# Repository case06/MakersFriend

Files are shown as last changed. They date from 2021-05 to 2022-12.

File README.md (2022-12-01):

# MakersFriend

[](
    https://opensourceecology.de)

This is the source repo for the "Maker's Friend" 3D-Printer-Projekt on

https://wiki.opensourceecology.de/Maker%27s_Friend

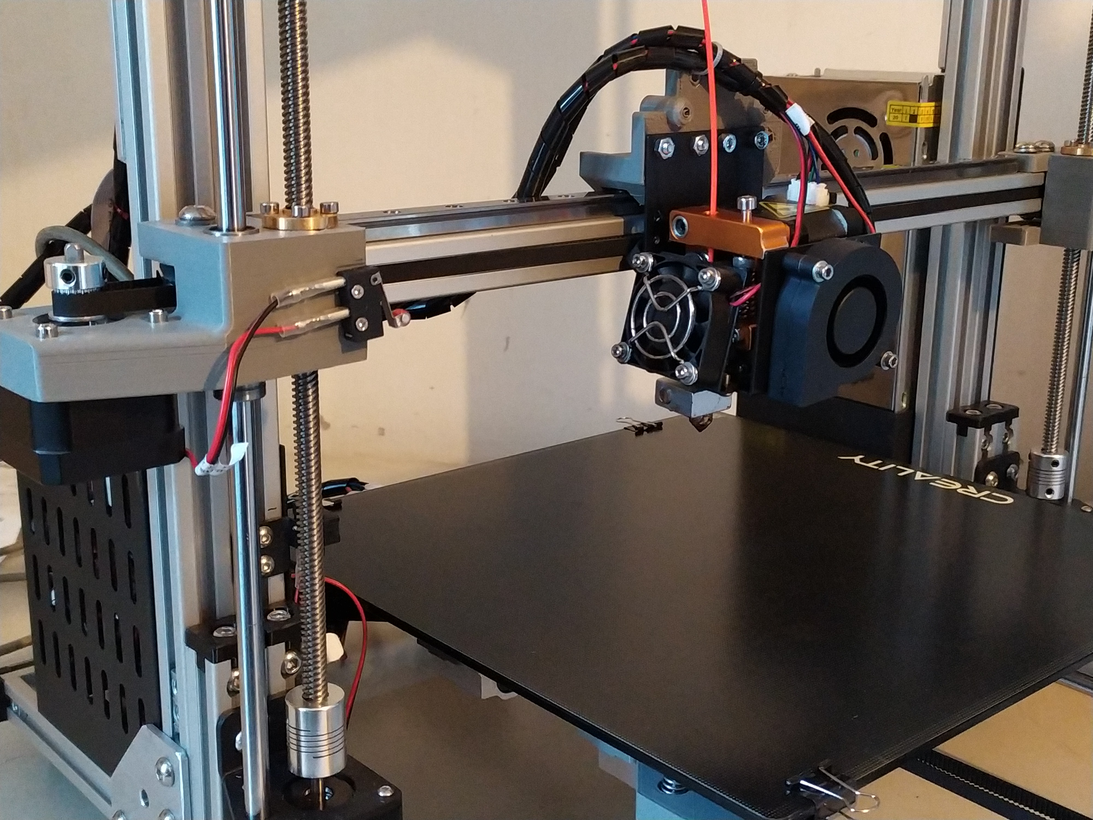
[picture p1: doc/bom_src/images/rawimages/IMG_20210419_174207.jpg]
Maker's Friend V.0.5
<p></p>

The projekt is based on the UniProKit 3D-part-library UPKlib V2.06, which is available at 

<a href="https://github.com/case06/upklib_v2"> https://github.com/case06/upklib_v2 </a>

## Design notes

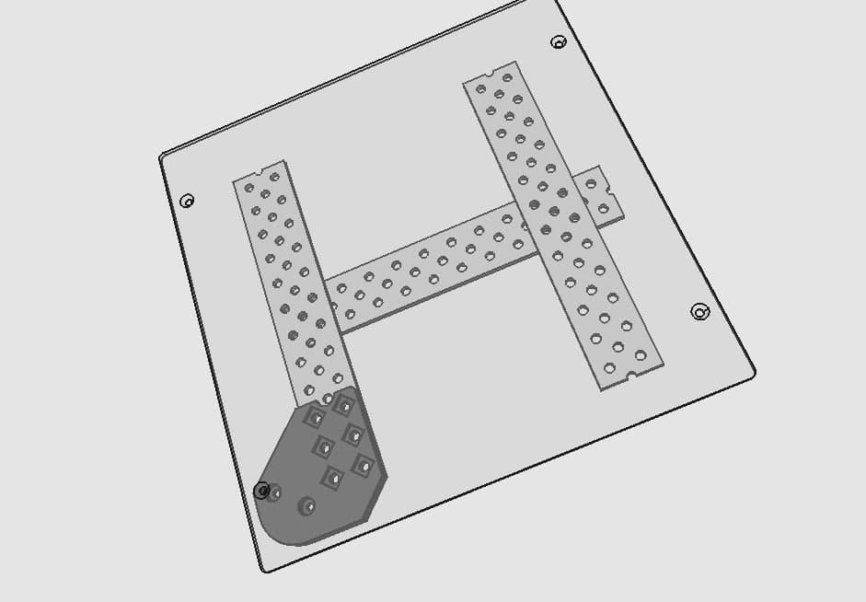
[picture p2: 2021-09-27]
cadfiles/images/heatbed/heatbed_ass.jpg

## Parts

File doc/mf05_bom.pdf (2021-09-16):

Seite 1

BOM Maker's Friend MF05 3D-Printer, UniProKit UPKlib V2.06

Partname | PartNo. | pcs. | Description | Pos | Supplier

UPKlib
tslot4 | 17092201 | 1 | T-Slot Nut 6, 40x20x20mm, framepart for tensioner | 1 | ML
tslot6 | 17092202 | 3 | T-Slot Nut 6, 60x20x20mm, distance holder | 2
tslot48 | 17092209 | 5 | T-Slot Nut 6, 480x20x20mm, distancer | 3
tslot8con | 17092220 | 2 | T-Slot Con, 480x20x20mm | 4
tslot40con_16 | | 4 | Framepart y-direction | 5
tslot48con_double | | 3 | Framepart x-direction | 6
m6x8 | 17092303 | 128 | 8mm, M6 ISO 7380, display- and spool-holder | 7
m6x12 | 17092304 | 62 | 12mm, M6 ISO 7380, mount holder | 8
m6x16 | 17092305 | 9 | 16mm, M6 ISO 7380, mount foot to frame | 9
m6x20 | 17092306 | 10 | 20mm, M6 ISO 7380, mount tslot6 | 10
m6x25cyl | 17092307 | 16 | 25mm, M6 DIN 7984, connect z-frame with y-base | 11
m6nutplate | 17092309 | 205 | für TSlot, Slot6, M6 | 12
m6washer | 17092310 | 42 | 6.4x12x1.6, DIN 125, display- and spool-holder | 13
m6nut | 17092308 | 4 | 5.6x10mm, M6 DIN934, mount z-floating-bearing | 14
m2x10 | | 2 | screws for mout limitswitch to holder | 15
m2.5x12ws | | 4 | M2.5 x 12 woodscrew | 16
m3x6 | | 17 | mount stepper | 17
m3x6cone | | 2 | mount mainboard on holder | 18
m3x8cyl | 21032807 | 20 | mount adapter on mgn12 | 19
m3x10cyl | 19070615 | 12 | mount stepper to holder | 20
m3x20cyl | 19082011 | 2 | pole for belt | 21
hammermutter_m3 | 21032803 | 16 | | 22

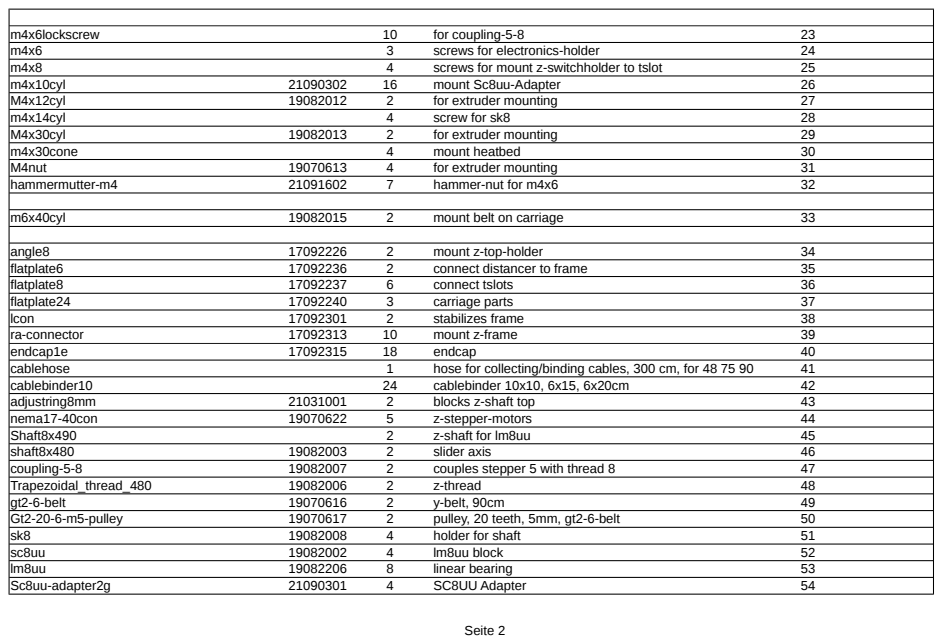
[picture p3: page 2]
Seite 2; m4x6lockscrew; for coupling-5-8; screws for electronics-holder; screws for mount z-switchholder to tslot; m4x10cyl; mount Sc8uu-Adapter; M4x12cyl; for extruder mounting; m4x14cyl; screw for sk8; M4x30cyl; m4x30cone; mount heatbed; M4nut; hammermutter-m4; hammer-nut for m4x6; m6x40cyl; mount belt on carriage; angle8; mount z-top-holder; flatplate6; connect distancer to frame; flatplate8; connect tslots; flatplate24; carriage parts; lcon; stabilizes frame; ra-connector; mount z-frame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

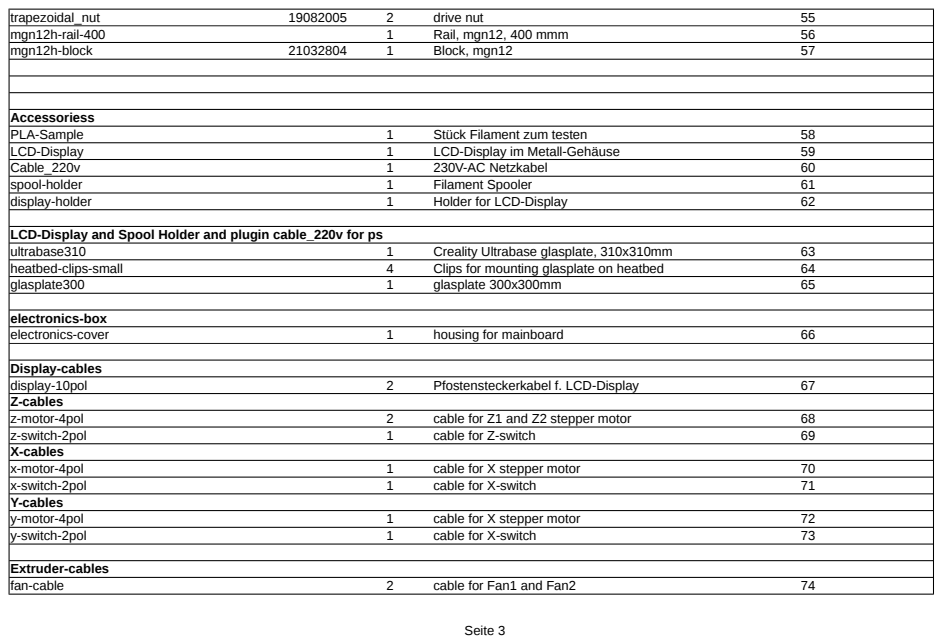
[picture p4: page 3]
Seite 3; trapezoidal_nut; drive nut; mgn12h-rail-400; Rail, mgn12, 400 mmm; mgn12h-block; Block, mgn12; Accessoriess; PLA-Sample; Stück Filament zum testen; LCD-Display; LCD-Display im Metall-Gehäuse; Cable_220v; 230V-AC Netzkabel; spool-holder; Filament Spooler; display-holder; Holder for LCD-Display; ultrabase310; Creality Ultrabase glasplate, 310x310mm; heatbed-clips-small; Clips for mounting glasplate on heatbed; glasplate300; glasplate 300x300mm; electronics-box; electronics-cover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

LCD-Display and Spool Holder and plugin cable_220v for ps

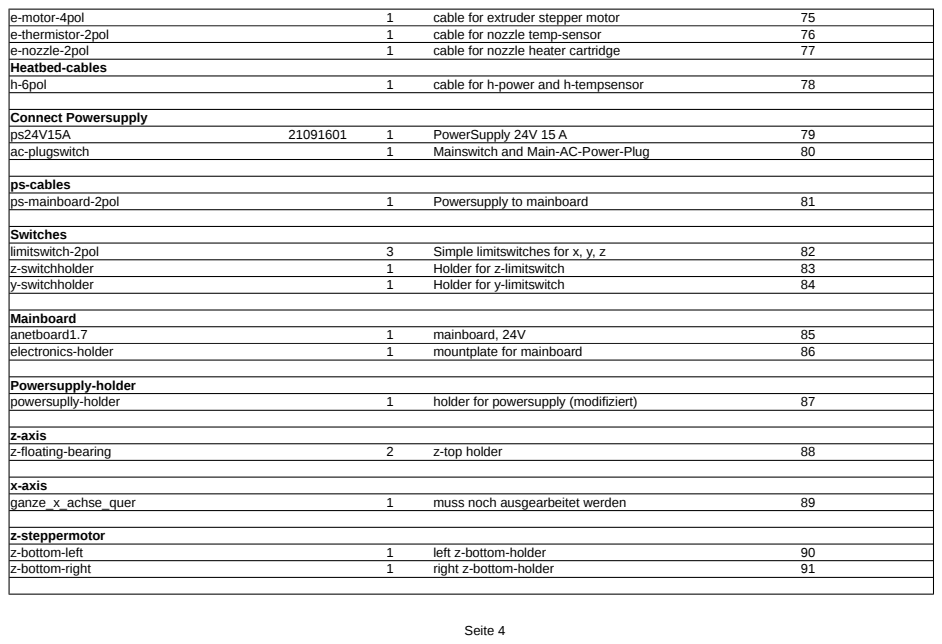
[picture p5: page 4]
Seite 4; e-motor-4pol; cable for extruder stepper motor; e-thermistor-2pol; cable for nozzle temp-sensor; e-nozzle-2pol; cable for nozzle heater cartridge; Heatbed-cables; h-6pol; cable for h-power and h-tempsensor; Connect Powersupply; PowerSupply 24V 15 A; ac-plugswitch; Mainswitch and Main-AC-Power-Plug; ps-cables; ps-mainboard-2pol; Powersupply to mainboard; Switches; limitswitch-2pol; Simple limitswitches for x, y, z; z-switchholder; Holder for z-limitswitch; y-switchholder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

Seite 5

Heatbed
heatbed300_276_209 | 1 | 300mm with hole-edge-distances 12 and 45.5 mm | 92
bedlevel-knob | 4 | adjust heatbed | 93
spring_8x25 | 4 | distance-spring for heatbed | 94
bedmount1d_left | 2 | bedmount left | 95
bedmount1d_right | 2 | bedmount right | 96

y-belt
belt-tensioner | 1 | belt-tensioner (assembly) | 97

y-steppermotor
nema17holder6mm | 1 | stepper holder, 6mm | 98

machine-feet
foot-35x24 | 4 | machine-foot, h 24 dia 35 depth 13 | 99
foot-38x25 | 0 | machine-foot, h 25 dia 38 depth 12

Extruder
extruder_adapter | 1 | extruder adapter to mount on mgn12 | 100

Mount idler
mf_idler | 1 | x-idler, z-carriage-right | 101
belt-tensioner | 1 | belt-tensioner (complete) | 102

Mount stepper
mf_steppermount | 1 | x-stepper, z-carriage-left | 103
804

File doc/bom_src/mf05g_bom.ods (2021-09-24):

BOM Maker's Friend MF05 3D-Printer, UniProKit UPKlib V2.06
Partname | PartNo. | pcs. | Description | Pos | Supplier
UPKlib
tslot4 | 17092201 | 1 | T-Slot Nut 6, 40x20x20mm, framepart for tensioner | 1 | ML
tslot6 | 17092202 | 3 | T-Slot Nut 6, 60x20x20mm, distance holder | 2
tslot48 | 17092209 | 5 | T-Slot Nut 6, 480x20x20mm, distancer | 3
tslot8con | 17092220 | 2 | T-Slot Con, 480x20x20mm | 4
tslot40con_16 |  | 4 | Framepart y-direction | 5
tslot48con_double |  | 3 | Framepart x-direction | 6
m6x8 | 17092303 | 128 | 8mm, M6 ISO 7380, display- and spool-holder | 7
m6x12 | 17092304 | 62 | 12mm, M6 ISO 7380, mount holder | 8
m6x16 | 17092305 | 9 | 16mm, M6 ISO 7380, mount foot to frame | 9
m6x20 | 17092306 | 10 | 20mm, M6 ISO 7380, mount tslot6 | 10
m6x25cyl | 17092307 | 16 | 25mm, M6 DIN 7984, connect z-frame with y-base | 11
m6nutplate | 17092309 | 205 | für TSlot, Slot6, M6 | 12
m6washer | 17092310 | 42 | 6.4x12x1.6, DIN 125, display- and spool-holder | 13
m6nut | 17092308 | 4 | 5.6x10mm, M6 DIN934, mount z-floating-bearing | 14
m2x10 |  | 2 | screws for mout limitswitch to holder | 15
m2.5x12ws |  | 4 | M2.5 x 12 woodscrew | 16
m3x6 |  | 17 | mount stepper | 17
m3x6cone |  | 2 | mount mainboard on holder | 18
m3x8cyl | 21032807 | 20 | mount adapter on mgn12 | 19
m3x10cyl | 19070615 | 12 | mount stepper to holder | 20
m3x20cyl | 19082011 | 2 | pole for belt | 21
hammermutter_m3 | 21032803 | 16 |  | 22
m4x6lockscrew |  | 10 | for coupling-5-8 | 23
m4x6 |  | 3 | screws for electronics-holder | 24
m4x8 |  | 4 | screws for mount z-switchholder to tslot | 25
m4x10cyl | 21090302 | 16 | mount Sc8uu-Adapter | 26
M4x12cyl | 19082012 | 2 | for extruder mounting | 27
m4x14cyl |  | 4 | screw for sk8 | 28
M4x30cyl | 19082013 | 2 | for extruder mounting | 29
m4x30cone |  | 4 | mount heatbed | 30
M4nut | 19070613 | 4 | for extruder mounting | 31
hammermutter-m4 | 21091602 | 7 | hammer-nut for m4x6 | 32
m6x40cyl | 19082015 | 2 | mount belt on carriage | 33
angle8 | 17092226 | 2 | mount z-top-holder | 34
flatplate6 | 17092236 | 2 | connect distancer to frame | 35
flatplate8 | 17092237 | 6 | connect tslots | 36
flatplate24 | 17092240 | 3 | carriage parts | 37
lcon | 17092301 | 2 | stabilizes frame | 38
ra-connector | 17092313 | 10 | mount z-frame | 39
endcap1e | 17092315 | 18 | endcap | 40
cablehose |  | 1 | hose for collecting/binding cables, 300 cm, for 48 75 90 64 and 20 cm | 41
cablebinder10 |  | 24 | cablebinder 10x10, 6x15, 6x20cm | 42
adjustring8mm | 21031001 | 2 | blocks z-shaft top | 43
nema17-40con | 19070622 | 5 | z-stepper-motors | 44
Shaft8x490 |  | 2 | z-shaft for lm8uu | 45
shaft8x480 | 19082003 | 2 | slider axis | 46
coupling-5-8 | 19082007 | 2 | couples stepper 5 with thread 8 | 47
Trapezoidal_thread_480 | 19082006 | 2 | z-thread | 48
gt2-6-belt | 19070616 | 2 | y-belt, 90cm | 49
Gt2-20-6-m5-pulley | 19070617 | 2 | pulley, 20 teeth, 5mm, gt2-6-belt | 50
sk8 | 19082008 | 4 | holder for shaft | 51
sc8uu | 19082002 | 4 | lm8uu block | 52
lm8uu | 19082206 | 8 | linear bearing | 53
Sc8uu-adapter2g | 21090301 | 4 | SC8UU Adapter | 54
trapezoidal_nut | 19082005 | 2 | drive nut | 55
mgn12h-rail-400 |  | 1 | Rail, mgn12, 400 mmm | 56
mgn12h-block | 21032804 | 1 | Block, mgn12 | 57
Accessoriess
PLA-Sample |  | 1 | Stück Filament zum testen | 58
LCD-Display |  | 1 | LCD-Display im Metall-Gehäuse | 59
Cable_220v |  | 1 | 230V-AC Netzkabel | 60
spool-holder |  | 1 | Filament Spooler | 61
display-holder |  | 1 | Holder for LCD-Display | 62
LCD-Display and Spool Holder and plugin cable_220v for ps
ultrabase310 |  | 1 | Creality Ultrabase glasplate, 310x310mm | 63
heatbed-clips-small |  | 4 | Clips for mounting glasplate on heatbed | 64
glasplate300 |  | 1 | glasplate 300x300mm | 65
electronics-box
electronics-cover |  | 1 | housing for mainboard | 66
Display-cables
display-10pol |  | 2 | Pfostensteckerkabel f. LCD-Display | 67
Z-cables
z-motor-4pol |  | 2 | cable for Z1 and Z2 stepper motor | 68
z-switch-2pol |  | 1 | cable for Z-switch | 69
X-cables
x-motor-4pol |  | 1 | cable for X stepper motor | 70
x-switch-2pol |  | 1 | cable for X-switch | 71
Y-cables
y-motor-4pol |  | 1 | cable for X stepper motor | 72
y-switch-2pol |  | 1 | cable for X-switch | 73
Extruder-cables
fan-cable |  | 2 | cable for Fan1 and Fan2 | 74
e-motor-4pol |  | 1 | cable for extruder stepper motor | 75
e-thermistor-2pol |  | 1 | cable for nozzle temp-sensor | 76
e-nozzle-2pol |  | 1 | cable for nozzle heater cartridge | 77
Heatbed-cables
h-6pol |  | 1 | cable for h-power and h-tempsensor | 78
Connect Powersupply
ps24V15A | 21091601 | 1 | PowerSupply 24V 15 A | 79
ac-plugswitch |  | 1 | Mainswitch and Main-AC-Power-Plug | 80
ps-cables
ps-mainboard-2pol |  | 1 | Powersupply to mainboard | 81
Switches
limitswitch-2pol |  | 3 | Simple limitswitches for x, y, z | 82
z-switchholder |  | 1 | Holder for z-limitswitch | 83
y-switchholder |  | 1 | Holder for y-limitswitch | 84
Mainboard
anetboard1.7 |  | 1 | mainboard, 24V | 85
electronics-holder |  | 1 | mountplate for mainboard | 86
Powersupply-holder
powersuplly-holder |  | 1 | holder for powersupply (modifiziert) | 87
z-axis
z-floating-bearing |  | 2 | z-top holder | 88
x-axis
ganze_x_achse_quer |  | 1 | muss noch ausgearbeitet werden | 89
z-steppermotor
z-bottom-left |  | 1 | left z-bottom-holder | 90
z-bottom-right |  | 1 | right z-bottom-holder | 91
Heatbed
heatbed300_276_209 |  | 1 | 300mm with hole-edge-distances 12 and 45.5 mm | 92
bedlevel-knob |  | 4 | adjust heatbed | 93
spring_8x25 |  | 4 | distance-spring for heatbed | 94
bedmount1d_left |  | 2 | bedmount left | 95
bedmount1d_right |  | 2 | bedmount right | 96
y-belt
belt-tensioner |  | 1 | belt-tensioner (assembly) | 97
y-steppermotor
nema17holder6mm |  | 1 | stepper holder, 6mm | 98
machine-feet
foot-35x24 |  | 4 | machine-foot, h 24 dia 35 depth 13 | 99
foot-38x25 |  | 0 | machine-foot, h 25 dia 38 depth 12
Extruder
extruder_adapter |  | 1 | extruder adapter to mount on mgn12 | 100
Mount idler
mf_idler |  | 1 | x-idler, z-carriage-right | 101
belt-tensioner |  | 1 | belt-tensioner (complete) | 102
Mount stepper
mf_steppermount |  | 1 | x-stepper, z-carriage-left | 103
 |  | 804

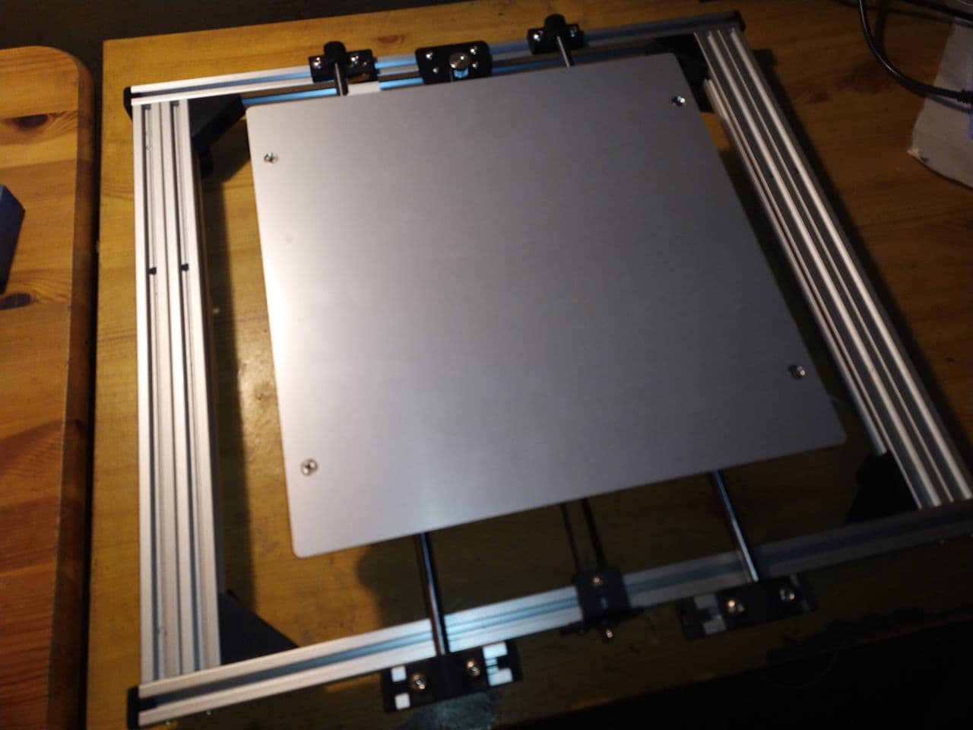
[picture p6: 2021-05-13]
doc/bom_src/images/y-achse_heatbed.jpg

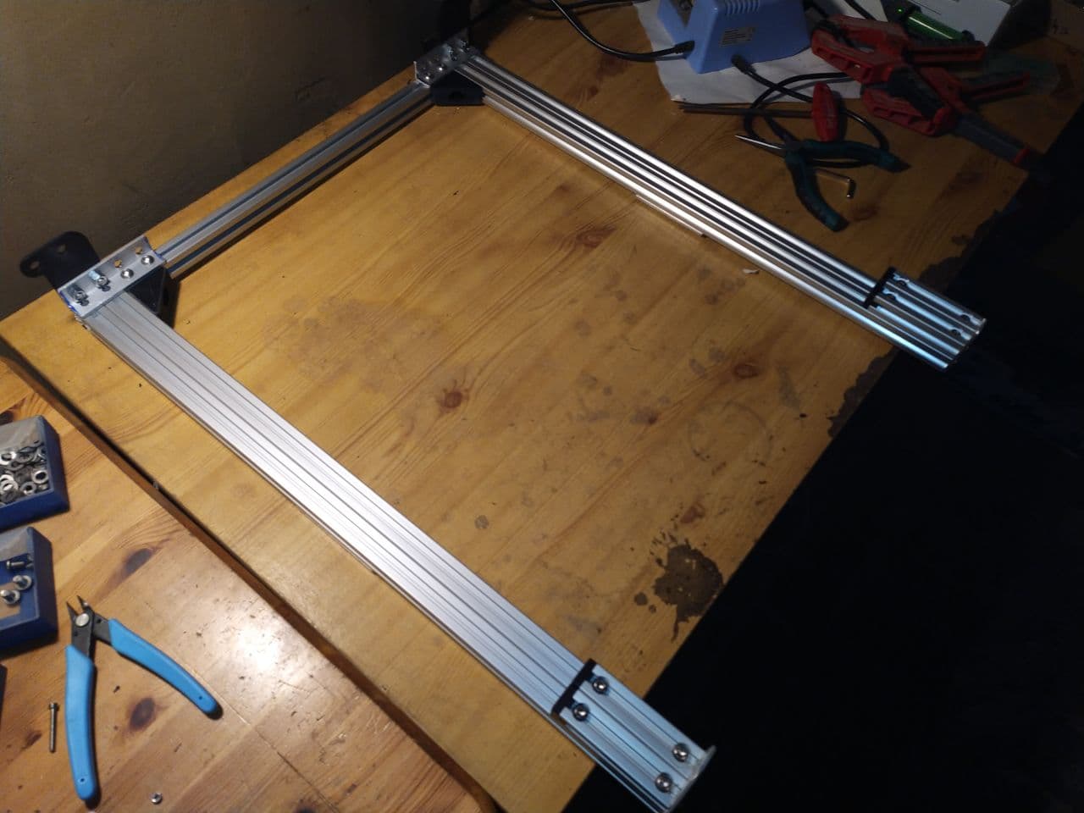
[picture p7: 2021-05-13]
doc/bom_src/images/z-frame.jpg

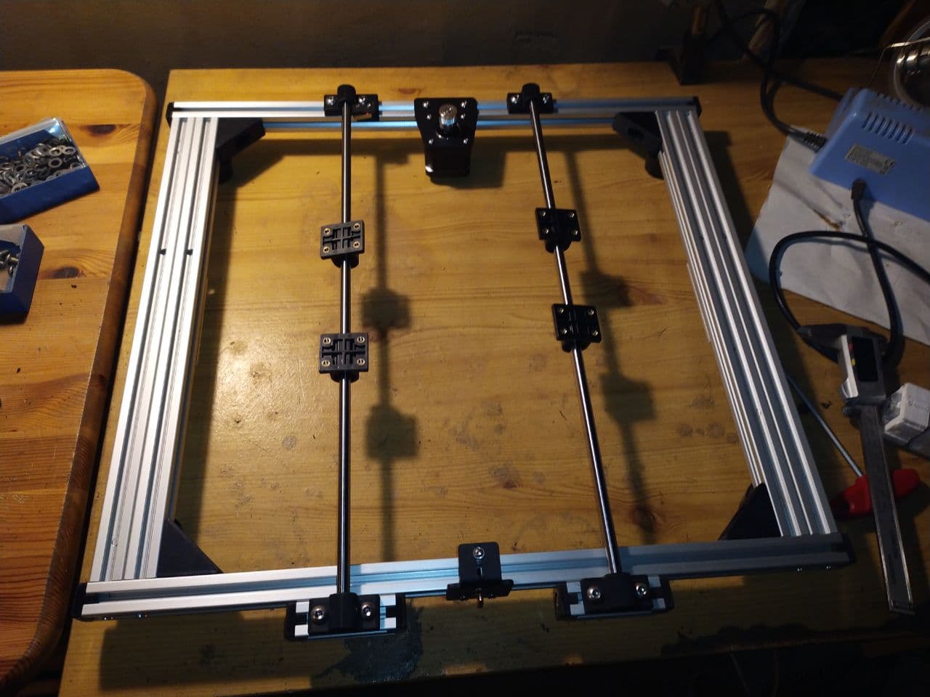
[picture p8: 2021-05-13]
doc/bom_src/images/y-axis1.jpg

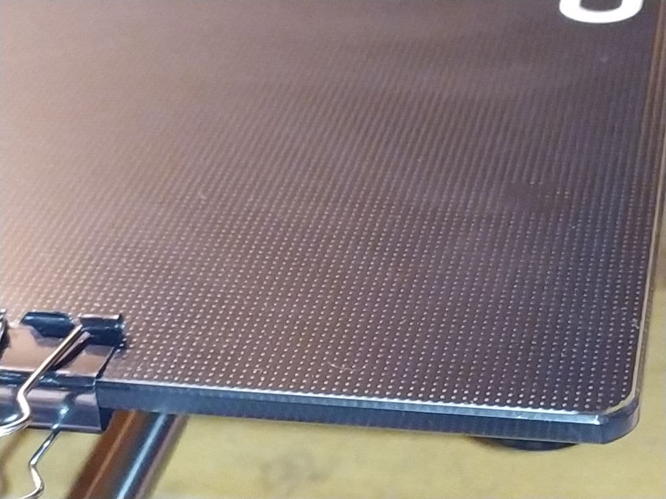
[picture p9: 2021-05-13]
doc/bom_src/images/y-axis_creality_closeup.jpg

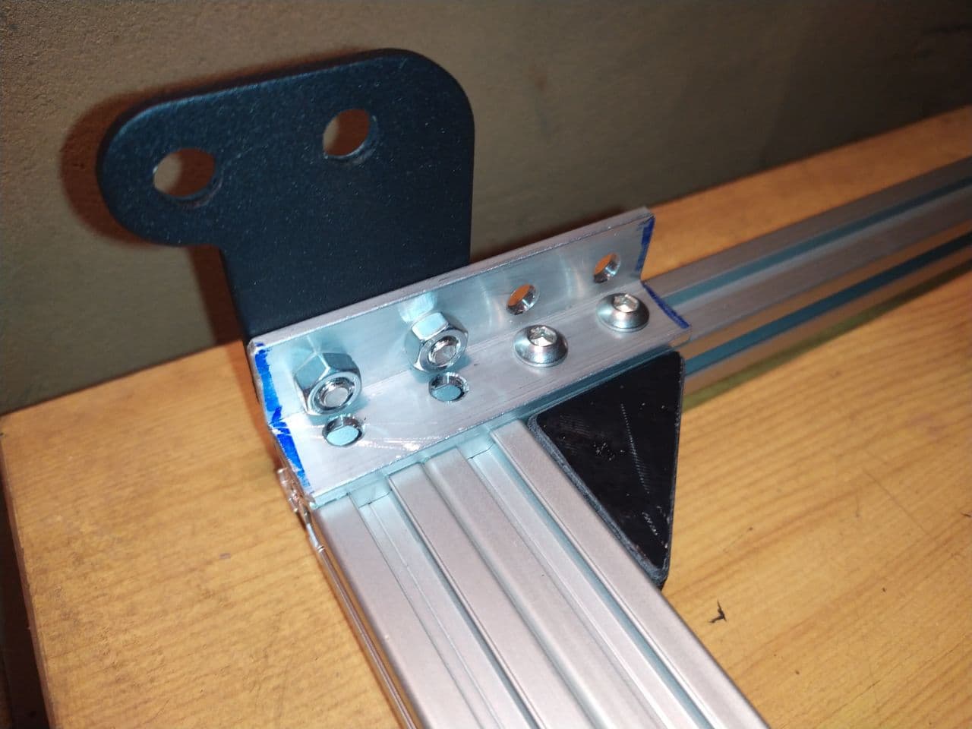
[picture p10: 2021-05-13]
doc/bom_src/images/zframe_corner.jpg

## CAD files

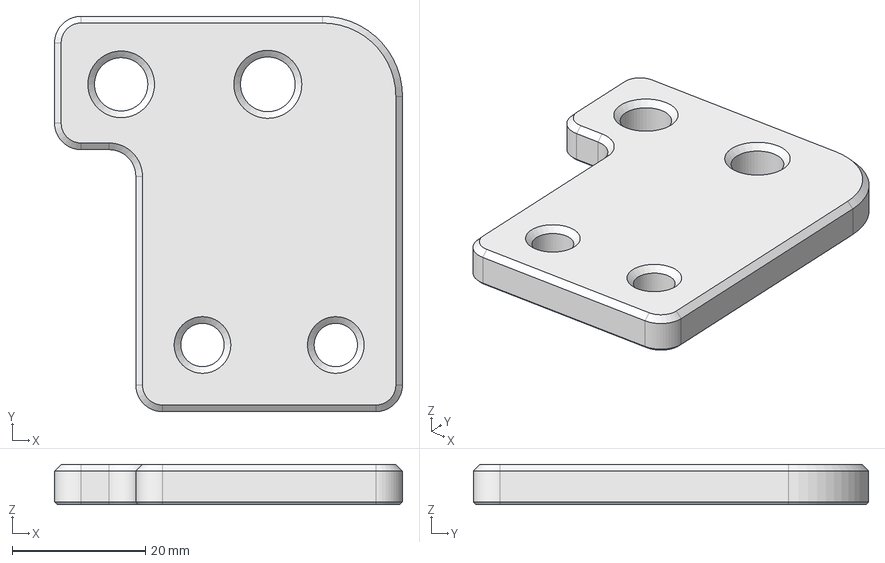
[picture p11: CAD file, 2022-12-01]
cadfiles/z-floating-bearing_cham1c.FCStd
52.2 x 59.3 x 6.00 mm

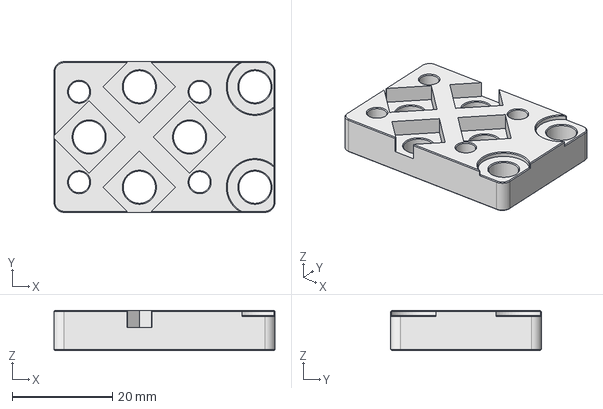
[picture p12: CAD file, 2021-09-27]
cadfiles/sc8uu-adapter2g_cham.FCStd
44.0 x 30.0 x 8.00 mm

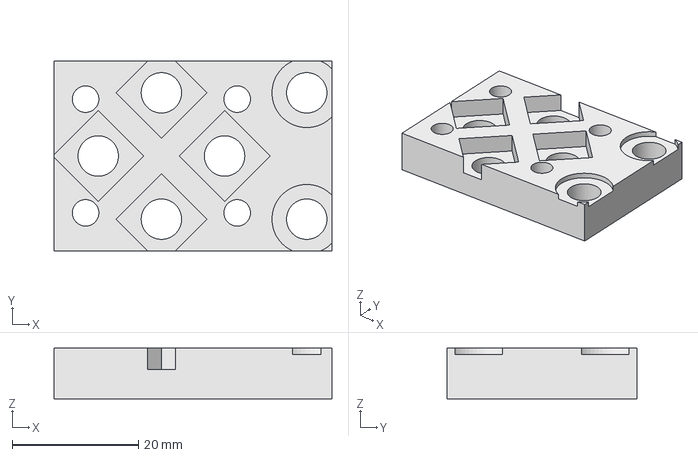
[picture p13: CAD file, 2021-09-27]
cadfiles/sc8uu-adapter2g.FCStd
44.0 x 30.0 x 8.00 mm

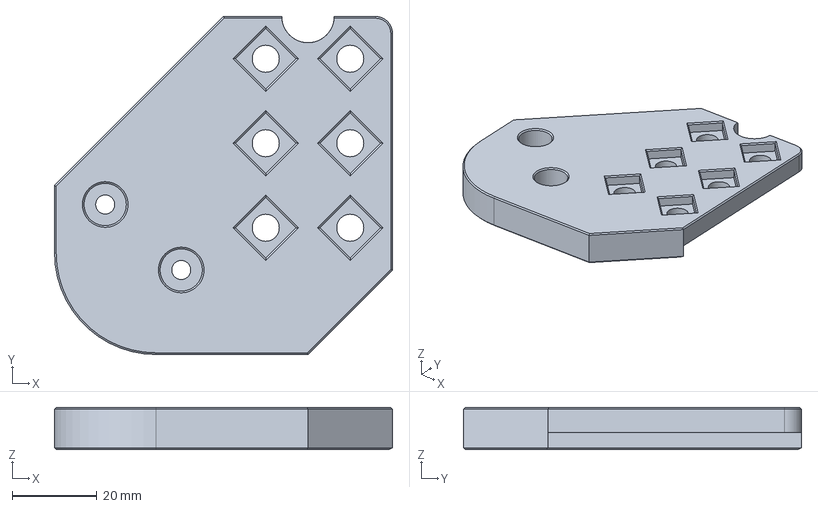
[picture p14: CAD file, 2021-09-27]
cadfiles/bedmount1e_cham.FCStd
80.0 x 80.0 x 10.0 mm

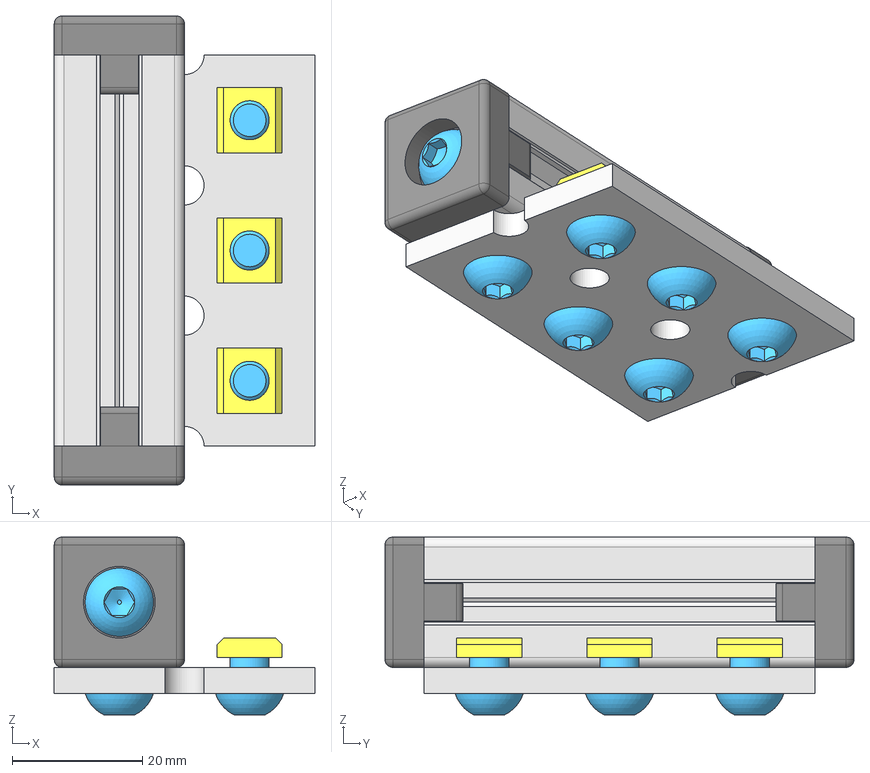
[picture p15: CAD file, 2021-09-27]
cadfiles/Mount-Y-Distancer.FCStd
40.0 x 72.0 x 27.3 mm
M6x8_006
m6nutplate_006
m6nutplate_002
M6x8_002
m6nutplate_004
M6x8_004
m6nutplate_005
M6x8_005
m6nutplate_003
M6x8_003
m6nutplate_001
M6x8_001
upk_flatplate60
M6x8_007
endcape001
endcape002
M6x8_008
Tslot6_001

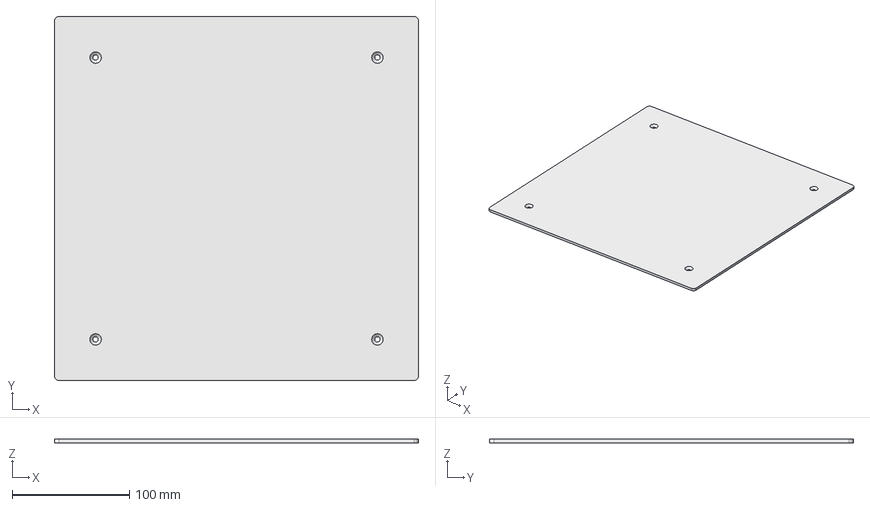
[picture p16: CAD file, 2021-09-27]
cadfiles/heatbed310.FCStd
310.0 x 310.0 x 3.00 mm

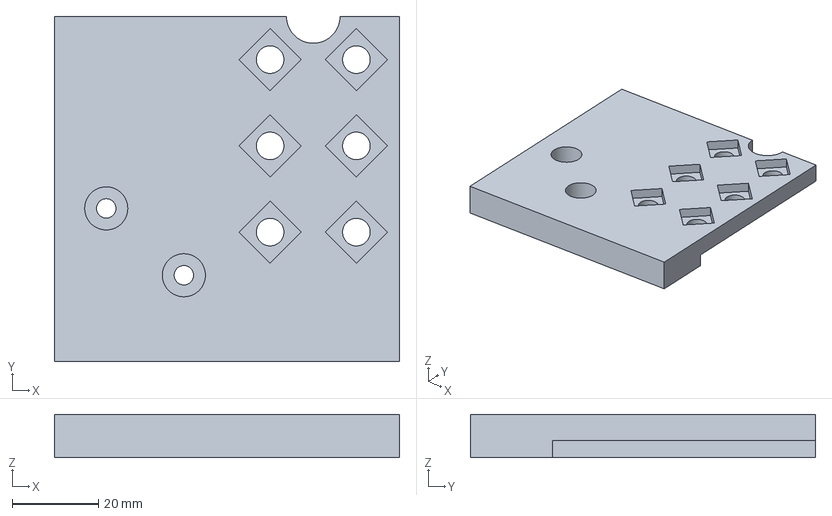
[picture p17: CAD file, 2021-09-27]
cadfiles/bedmount1e.FCStd
80.0 x 80.0 x 10.0 mm

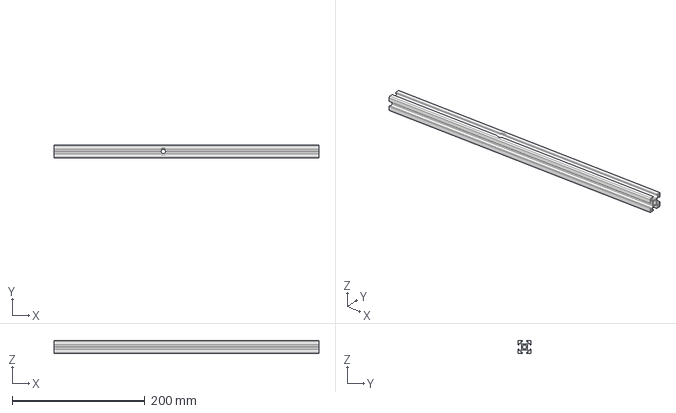
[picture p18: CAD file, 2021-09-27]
cadfiles/Tslot40-mit-Bohrung-165mm.FCStd
400.0 x 20.0 x 20.0 mm

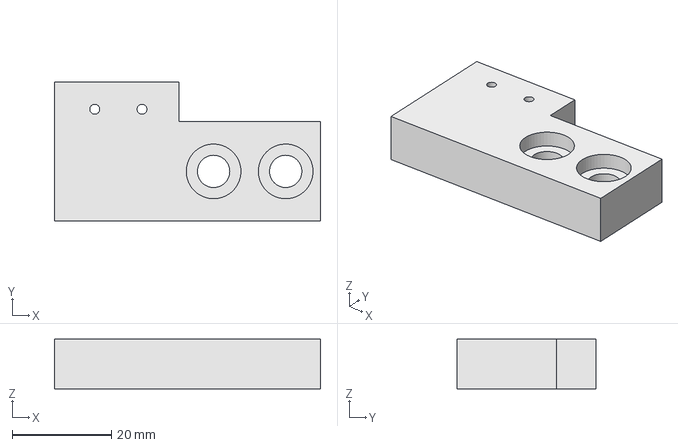
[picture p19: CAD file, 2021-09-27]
cadfiles/y-switchholder.FCStd
53.5 x 28.0 x 10.0 mm

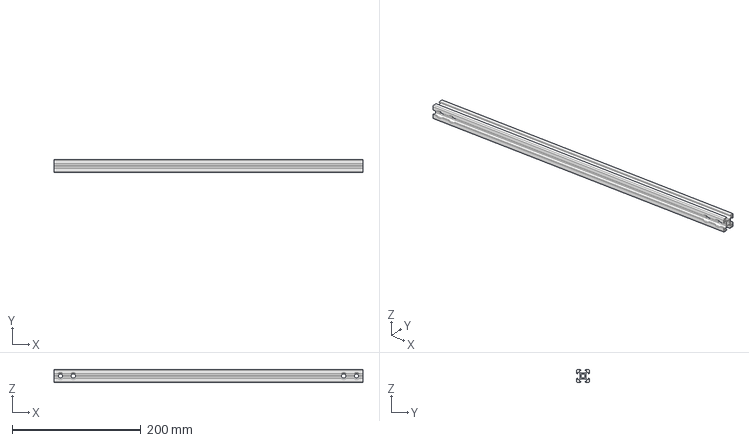
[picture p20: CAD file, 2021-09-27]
cadfiles/Tslot48con-doppelt.FCStd
480.0 x 20.0 x 20.0 mm

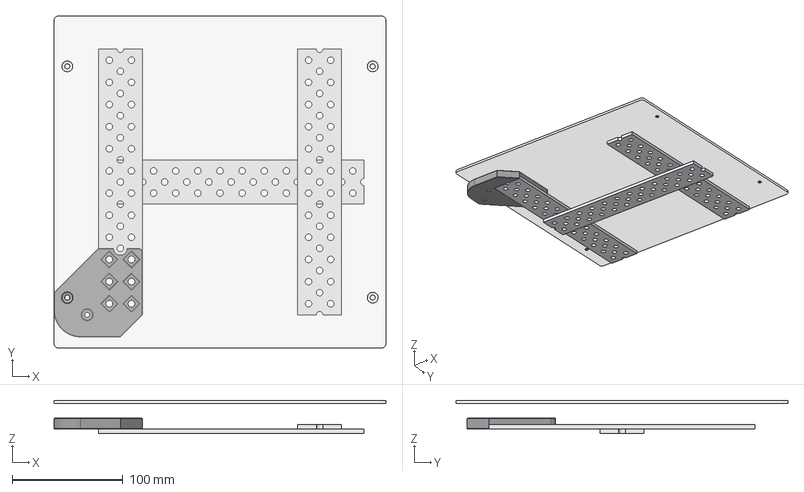
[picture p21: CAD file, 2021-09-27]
cadfiles/headbed_ass1d.FCStd
300.0 x 300.0 x 30.0 mm
upk_flatplate240
upk_flatplate241
upk_flatplate242
heatbed300
bedmount1d

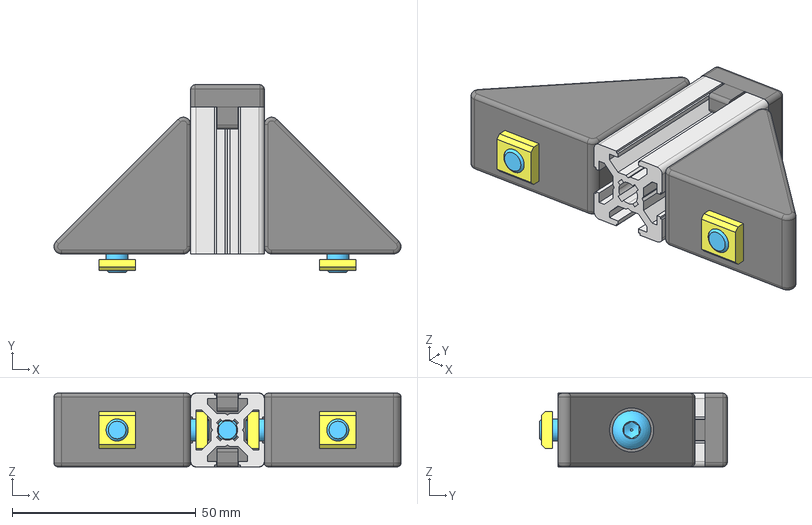
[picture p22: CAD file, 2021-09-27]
cadfiles/Mount-tensioner-framepart.FCStd
94.3 x 51.0 x 20.0 mm
endcape
M6x8
Tslot4
dreieck1h_Fillet_002
M6x12-Screw002
m6nutplate002
M6x12-Screw003
m6nutplate003
dreieck1h_Fillet_001
M6x12-Screw
m6nutplate
M6x12-Screw001
m6nutplate001

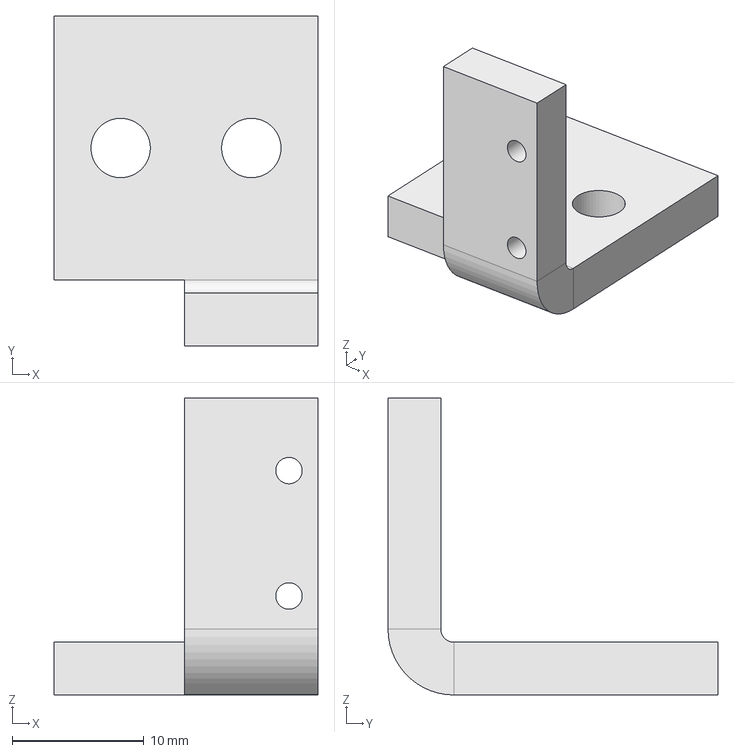
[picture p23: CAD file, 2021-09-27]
cadfiles/z-switchholder.FCStd
20.0 x 25.0 x 22.5 mm

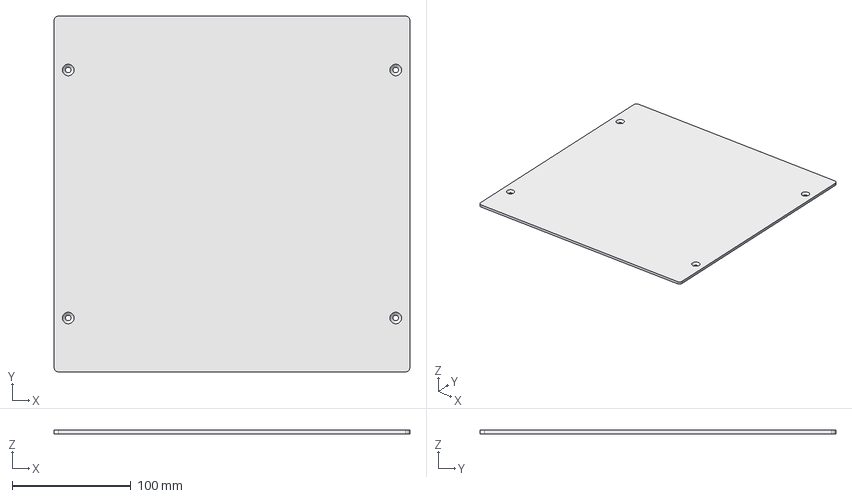
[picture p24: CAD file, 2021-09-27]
cadfiles/heatbed300.FCStd
300.0 x 300.0 x 3.00 mm

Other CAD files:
cadfiles/T-Slot-Skizze.FCStd
cadfiles/3d-Drucker-Rahmen_005a.FCStd
cadfiles/upk_flatplate60+m6x8screwnutplate-Baugruppe.FCStd

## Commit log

2021-09-16 added assembly guide
    [mf05_subassemblie_bom_guide.ods, mf05b_bom.ods, mf05b_subassemblie_bom_guide.ods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]
2021-09-16 minor changes
    [mf05g_bom.ods]
2021-09-27 added cadfiles
    [3d-Drucker-Rahmen_005a.FCStd, Mount-Y-Distancer.FCStd, Mount-tensioner-framepart.FCStd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]
2022-12-01 added oseg custombadge
    [z-floating-bearing.FCStd, z-floating-bearing_cham1c.FCStd]
